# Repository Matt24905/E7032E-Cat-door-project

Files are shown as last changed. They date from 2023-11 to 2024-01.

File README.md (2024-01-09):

# E7032E-Cat-door-project
Universal low power antennas for pet microchips
<p>
  
**Project members:** <br>
Matilda Segerlund, matseg-9@student.ltu.se  <br>
Nebez Rashid, nabras-9@student.ltu.se <br>
Anders Hagström, hagane-9@student.ltu.se <br>
Agnes Lindsten, agelin-7@student.ltu.se <br>
Arvid Mattsson, arvmat-9@student.ltu.se <br>
Jakob Ekvall, jakekv-9@student.ltu.se <br>

Report to do list : https://docs.google.com/spreadsheets/d/1z1Jb6kbTAtdWHH0EG9lIYJ78wvPaeEFzT7mHL56cxgM/edit?usp=sharing

Link to report: [https://www.overleaf.com/read/vsyjcxfwmcch](https://www.overleaf.com/read/vsyjcxfwmcch) <br>

Link to presentation: https://docs.google.com/presentation/d/1uJuHqVPSid_aY_8UZ3XwjzQQK3nhx3rkxRstLh7R2MM/edit?usp=sharing

Link to WBS/project plan: https://docs.google.com/spreadsheets/d/1j_RC8x2nzi24WwkHtlm5jIMLNItzt1e427vKWdE4rbc/edit?usp=sharing <br>

**Background:** <br>
Since the mid-80's, microchip implants have been used in pets and livestocks to identify them. These implements are a little larger than a rice grain. They are passive RFID chips that must be remotely powered to receive the identification information. They are progressively been required by law. <br>

Beside legal identification, these microchips can be used to identify a pet when they want to be fed (i.e., not allow an obese pet to over eat) or to let them enter or exit their home. The latter prevents "foreign" cats to enter homes where they have no business to be in. <br>

There is a problem when the orientation of the scanner's antenna and the microchips are not aligned. The pet doors and feeders are battery powered and fixed. The former results in not enough power to retrieve the information, while the latter could have been a solution by rotating the antenna (or chip inside the pet). <br>

**Objective:** <br>
The project is simply to design a low power antenna that allows the microchip to be read whatever is its relative orientation. <br>

**Key features:** <br>
* **Compatibility:** The solution must be ISO 11784 and ISO 11785 compliant. That is, it must be able to be optimized for 134.2 kHz, but should also be able to read at 125 kHz for US microchips.
* **Low power:** The cat door should work 6 months on four AA batteries.
* **Size:** It should fit in a pet door.
* **Temperature:** It should function in temperatures from -20°C to 60°C.
* **Internet ready:** The solution should be able to integrate a secured solution that connects to the Internet. This could include near field communication (NFC), bluetooth, and WiFi solutions. 

</p>

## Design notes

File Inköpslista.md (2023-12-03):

| Date | Item |Amount | Link | Approved/ordered | Received | 
|---|---|---|---|---|---|
| 3/10 |Raspberry Pico W | 2 |https://www.electrokit.com/produkt/raspberry-pi-pico-wh/ | <ul><li>[X] </li></ul>  | <ul><li>[X] </li></ul> | 
| 6/10 |Antenna wire | 1 |[https://www.elfa.se/sv/koppartrad-008mm-o0-1mm-200g-block-cul-200-10/p/15550334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](https://www.elfa.se/sv/koppartrad-2mm-o0-5mm-200g-block-cul-200-50/p/15550340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) | <ul><li>[x] </li></ul>  | <ul><li>[x] </li></ul> | 
| 6/10 |PCB  things from Farnell |34 items| I send an email with the basket and its also on git as "ShoppingBasket" | <ul><li>[x] </li></ul>  | <ul><li>[x] </li></ul> | 
| 30/10 |OP amp rekommenderad |1 items| https://se.farnell.com/microchip/mcp6l01ut-e-ot/ic-op-amp-1-0mhz-1-8v-sot23-5/dp/1852141?st=mcp6l01 | <ul><li>[x] </li></ul>  | <ul><li>[x] </li></ul> | 
| 30/10 |OP amp till breadboard |1 items| https://se.farnell.com/texas-instruments/lm358p/ic-op-amp-dual-dip8-358/dp/3117074?st=lm358  | <ul><li>[x] </li></ul>  | <ul><li>[x] </li></ul> | 
| 25/11 |ATtiny85 |1 items| [ ATTINY85 Farnell ](https://se.farnell.com/microchip/attiny85-20pu/mcu-8bit-attiny-20mhz-dip-8/dp/1455162?st=attiny)  | <ul><li>[x] </li></ul>  | <ul><li>[x] </li></ul> | 
| 03/12 |ATtiny84 |1 items| [ ATTINY84 Farnell ](https://se.farnell.com/microchip/attiny84a-pu/mcu-8bit-attiny-20mhz-dip-14/dp/1972172?st=attiny84)  | <ul><li>[x] </li></ul>  | <ul><li>[x] </li></ul> | 
| 03/12 |BJT |5 items| [ 2N3904 Farnell ](https://se.farnell.com/multicomp/2n3904/transistor-npn-to-92/dp/1574370?st=2n3904)  | <ul><li>[x] </li></ul>  | <ul><li>[x] </li></ul> | 

Företag som vi kan beställa ifrån: <br>
https://se.farnell.com/ <br>
https://www.rs-online.com/ <br>
https://www.elfa.se/sv/<br>

Ifall det inte finns på någon av de övre. <br>
https://www.digikey.se/en

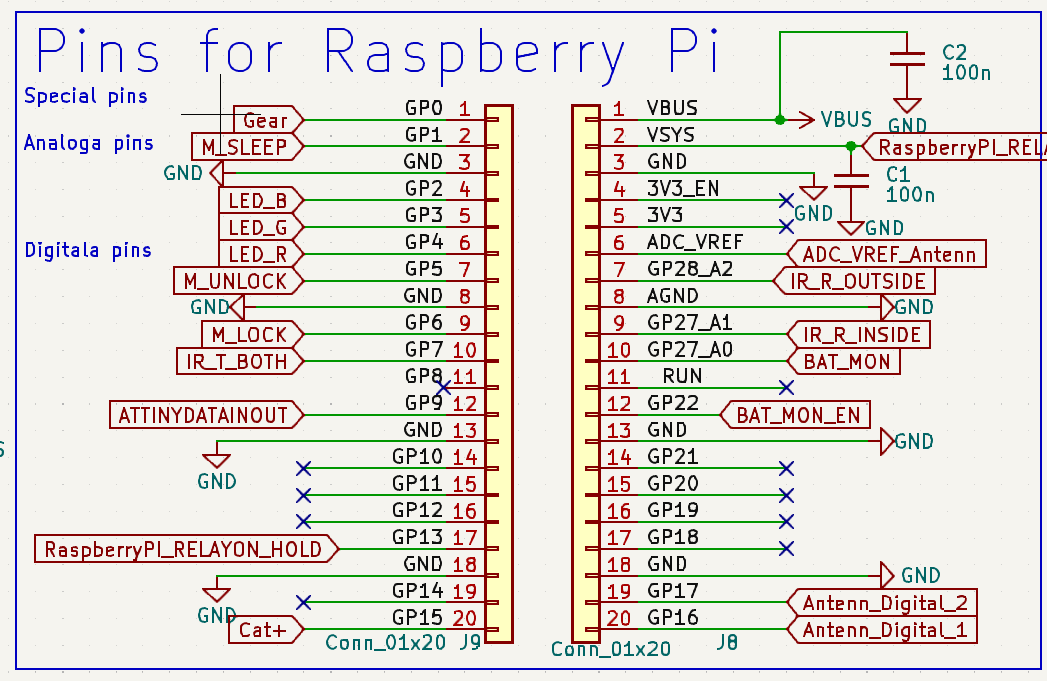
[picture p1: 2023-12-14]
Hardware/kicad.PNG

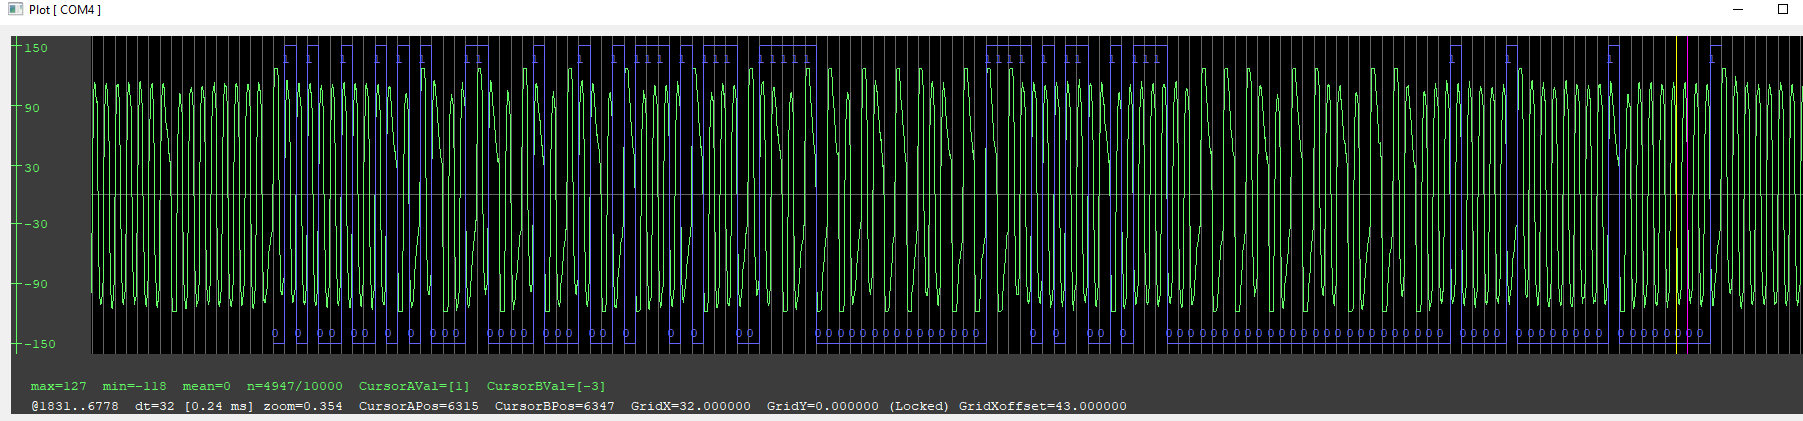
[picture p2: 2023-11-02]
Software/Proxmark3/Petchip read proxmark3 PLOT.PNG

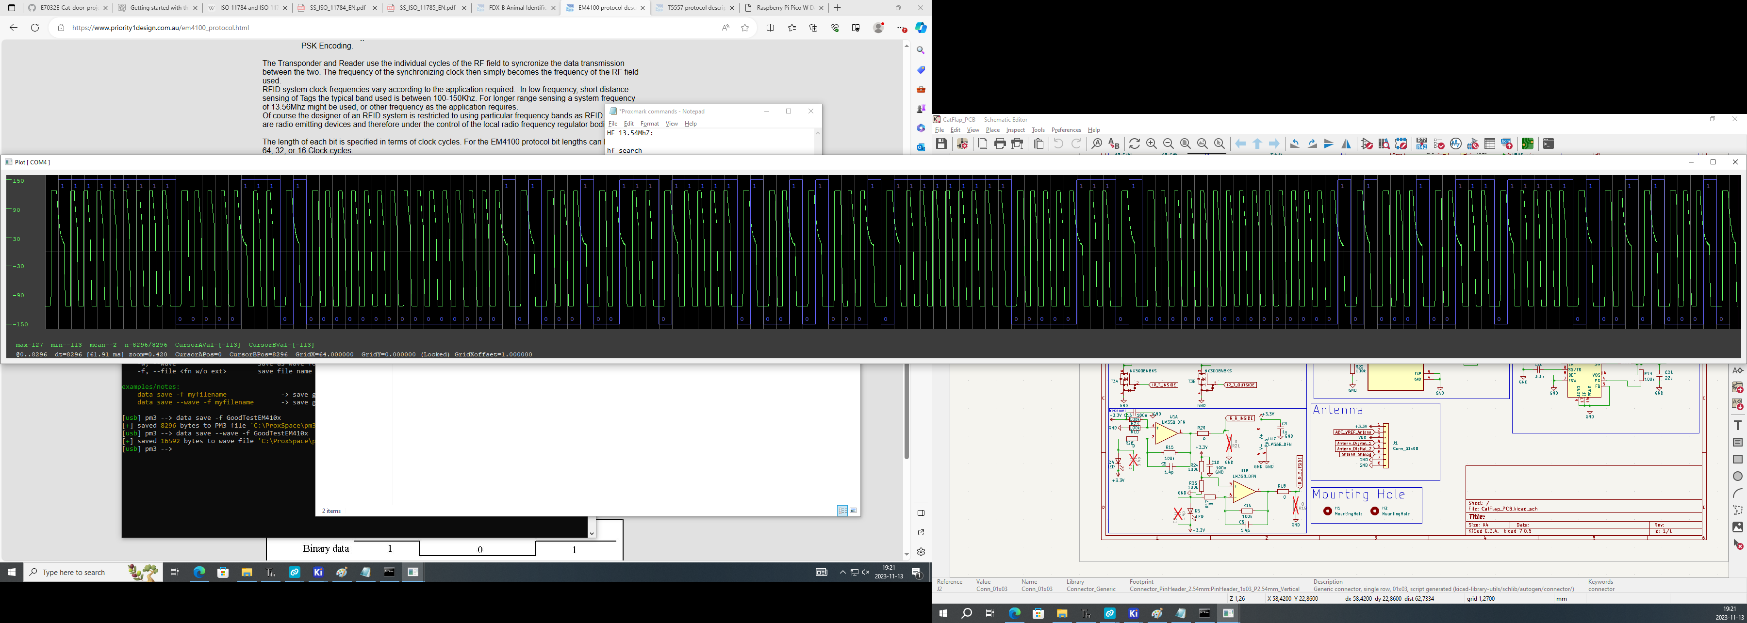
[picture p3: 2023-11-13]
Software/Proxmark3/Paint image of GoodEm410x file.png

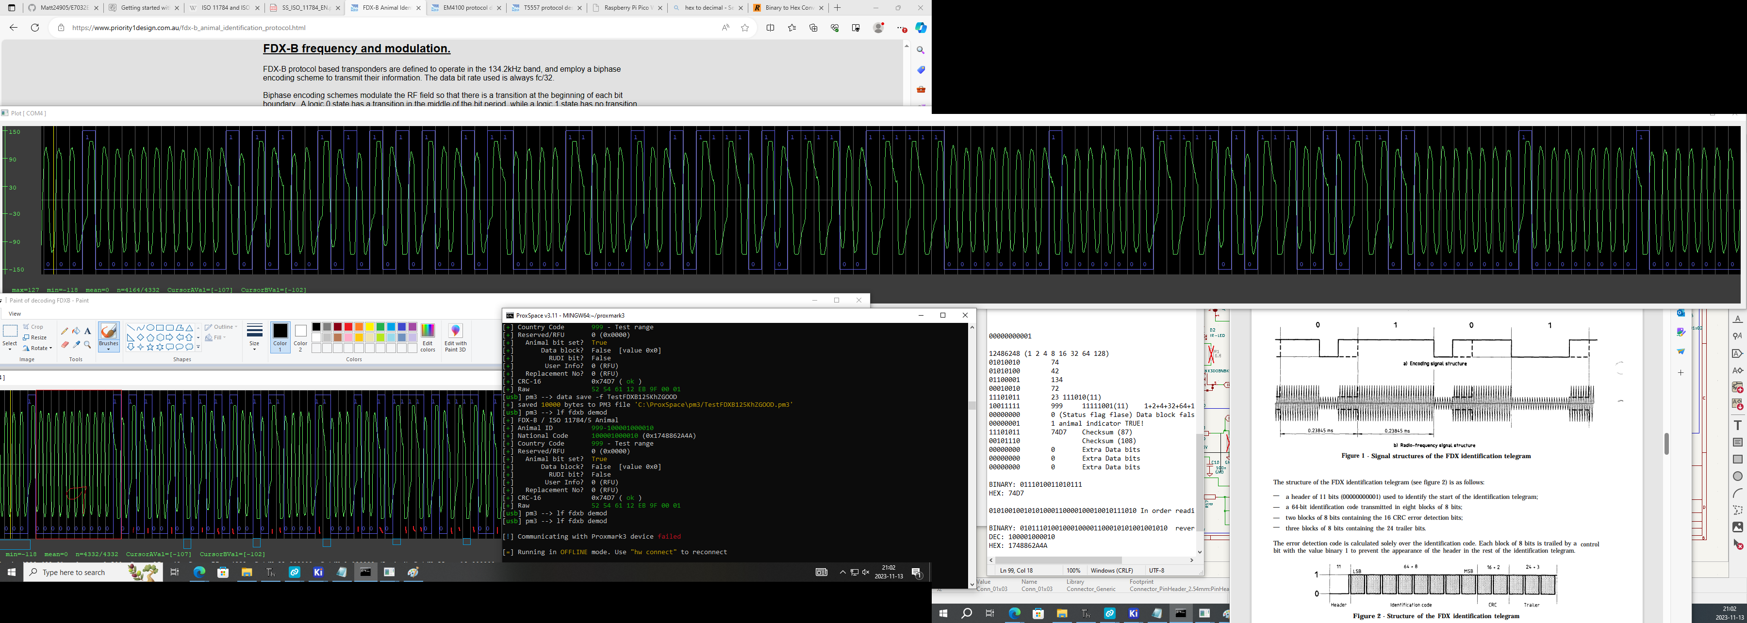
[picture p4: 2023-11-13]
Software/Proxmark3/EVERYTHING FDXB.png

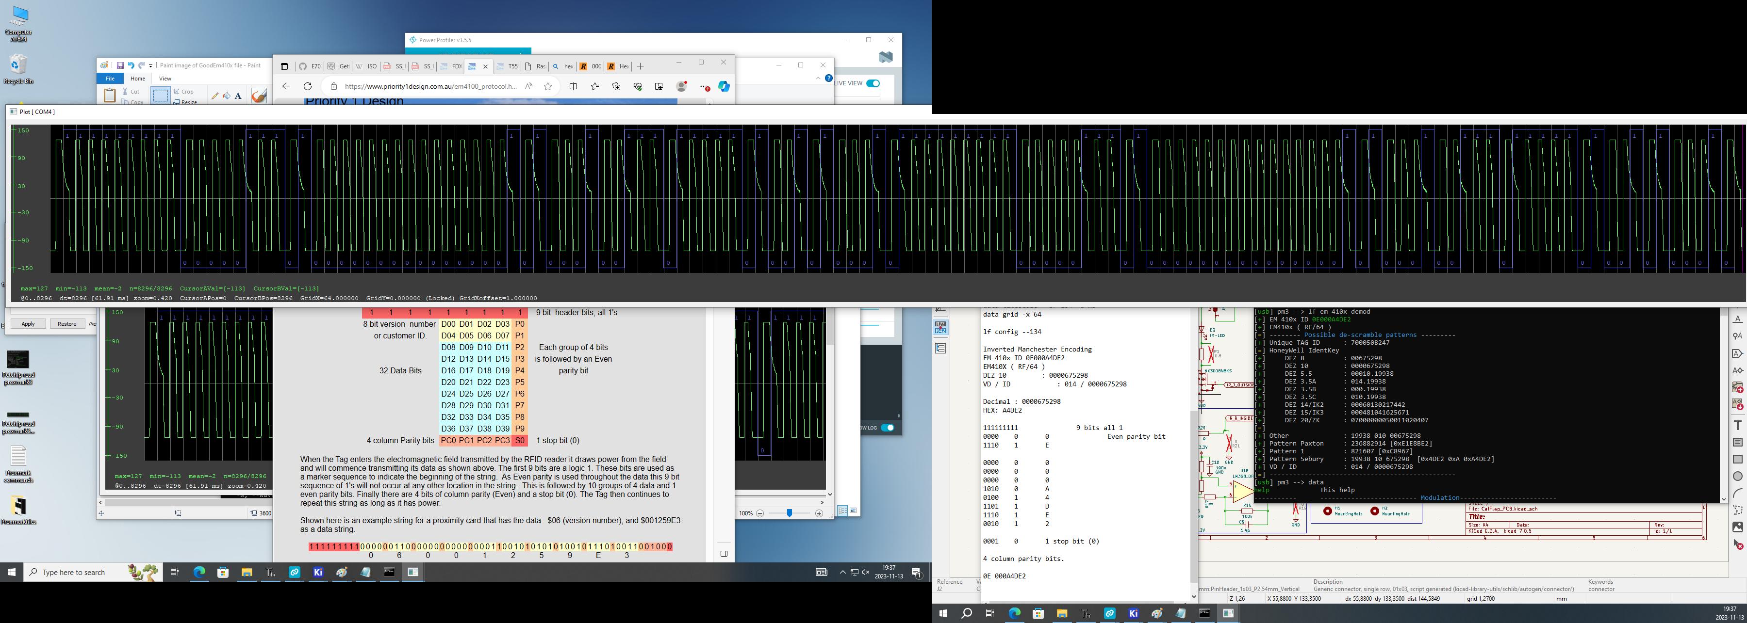
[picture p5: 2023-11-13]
Software/Proxmark3/Paint image of GoodEm410xdata EVERYTHING.png

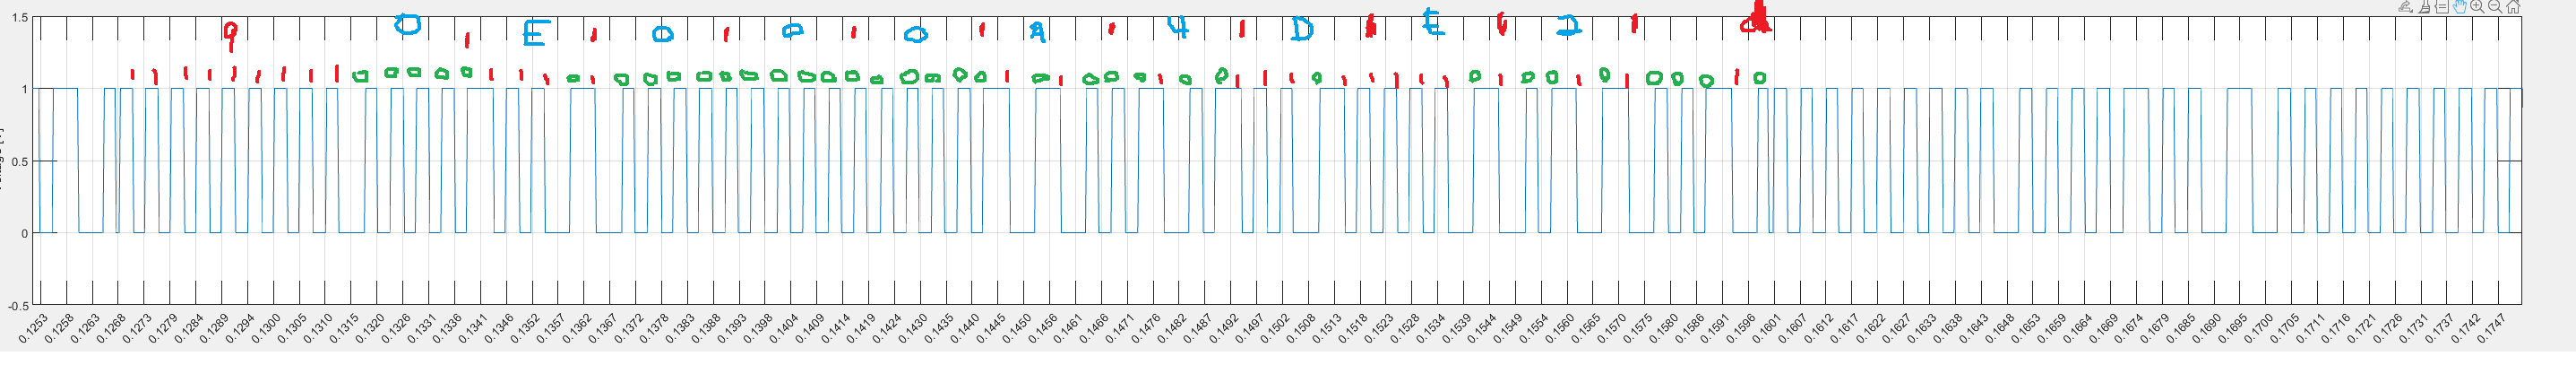
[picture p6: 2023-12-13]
Software/Matlab/em_txt file as 0E000A4DE2.png

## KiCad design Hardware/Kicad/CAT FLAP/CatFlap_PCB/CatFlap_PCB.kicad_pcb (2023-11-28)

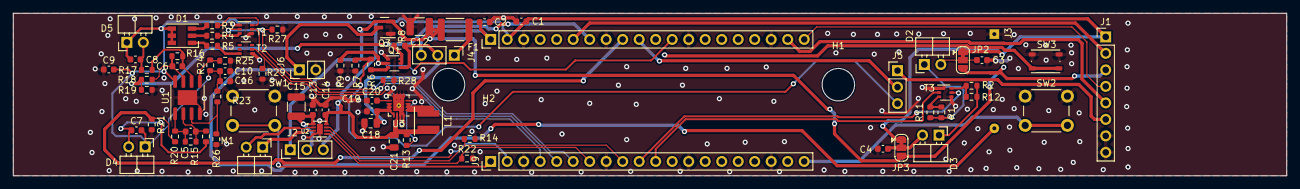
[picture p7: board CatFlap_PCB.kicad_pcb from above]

Board: 2 copper layers, 196.0 x 25.0 mm, 79 parts (0 on the bottom side), 54 nets.

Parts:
C1, C2, C10, C13, C14, C16, C19: 100n; C_0603_1608Metric
C3, C4, C9: 1u; C_0603_1608Metric
C5, C6, C7, C8: 1.4p; C_0603_1608Metric
C12, C15: 100u; C_1210_3225Metric
C18: 10u; C_0805_2012Metric
C20: 3.3n; C_0603_1608Metric
C21: 22u; C_0805_2012Metric
D1: LED_RGB; LED_RGB_PLCC-6
D2, D3: IR-LED; PinHeader_1x02_P2.54mm_Horizontal
D4, D5: LED; PinHeader_1x02_P2.54mm_Horizontal
F1: Polyfuse; Fuse_1812_4532Metric
H1, H2: MountingHole; MountingHole_5mm
J1: Conn_01x08; PinHeader_1x08_P2.54mm_Vertical
J2, J5: Conn_01x03; PinHeader_1x03_P2.54mm_Vertical
J3: Battery pack; BatteryHolder_MPD_BH-18650-PC2
J4: Conn_01x03_Socket; PinHeader_1x03_P2.54mm_Vertical
J6: Conn_01x02; PinHeader_1x02_P2.54mm_Vertical
J8, J9: Conn_01x20; PinHeader_1x20_P2.54mm_Vertical
JP2, JP3: SolderJumper_3_Bridged12; SolderJumper-3_P1.3mm_Bridged12_RoundedPad1.0x1.5mm
L1: 2.2u; L_Coilcraft_XxL4020
M1: Motor_DC; PinHeader_1x02_P2.54mm_Horizontal
Q1: NX3008CBKS; SOT-363_SC-70-6
Q3: Q_PMOS_GSD; SOT-23
R1, R2, R11, R12: 6.8; R_0603_1608Metric
R3: 68; R_0603_1608Metric
R4: 22; R_0603_1608Metric
R5: 10; R_0603_1608Metric
R6, R27, R28, R29: 330k; R_0603_1608Metric
R7: 220k; R_0603_1608Metric
R8, R9: 1meg; R_0603_1608Metric
R10, R17, R18, R19, R20, R21: 0; R_0603_1608Metric
R13, R14, R15, R16, R22, R23, R24, R25, R26: 100k; R_0603_1608Metric
SW1, SW2: SW_Push; SW_PUSH_6mm_H4.3mm
SW3: SW_Push; SW_Push_1P1T_NO_Vertical_Wuerth_434133025816
T1, T2, T3: NX3008NBKS; SOT-363_SC-70-6
U1: LM358_DFN; SOIC-8-1EP_3.9x4.9mm_P1.27mm_EP2.29x3mm
U2: DRV8837DSGR; SON50P200X200X80-9N
U3: TPS62132; VQFN-16-1EP_3x3mm_P0.5mm_EP1.68x1.68mm_ThermalVias

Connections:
+3.3V: C1.2, C7.2, C8.2, C9.2, C10.2, C14.2, C16.2, C21.2, D1.4 (BA), D1.5 (GA), D1.6 (RA), D4.1 (K), D5.1 (K), J1.1, J2.3, J8.2, JP2.1 (A), JP3.1 (A), L1.2, R13.2, R23.1, R24.1, U1.8 (V+), U2.8 (VCC), U3.14 (VOS)
/GP27_A0: J5.2, J8.10
ADC_VREF_Antenn: J1.2, J8.6
Antenn_Analog: J1.6, J5.1
Antenn_Digital_1: J1.4, J8.20
Antenn_Digital_2: J1.5, J8.19
BAT_MON: J5.3, R6.2, R7.1
BAT_MON_EN: J8.12, Q1.2 (G), R9.1
Cat+: J9.20, SW2.2
GND: C1.1, C2.1, C3.1, C4.1, C9.1, C10.1, C12.1, C13.1, C14.1, C15.1, C16.1, C18.1, C19.1, C20.2, C21.1, J1.7, J1.8, J3.1 (GND), J6.2, J8.3, J8.8, J8.13, J8.18, J9.3, J9.8, J9.13, J9.18, Q1.1 (S), Q3.1 (G), R7.2, R9.2, R14.2, R19.2, R21.2, R22.1, R25.2, R26.1, R27.1, R28.1, R29.1, SW1.1, SW2.1, SW3.1, T1.1, T1.4, T2.1, T3.1, T3.4, U1.4 (V-), U1.9 (PAD), U2.4 (GND), U2.9 (EXP), U3.5 (FB), U3.6 (AGND), U3.7 (FSW), U3.8 (DEF), U3.15 (PGND), U3.16 (PGND), U3.17 (EP)
Gear: J9.1, SW1.2
IR_R_INSIDE: J8.9, R20.1, R21.1
IR_R_OUTSIDE: J8.7, R18.1, R19.1
IR_T_INSIDE: J9.11, T3.2
IR_T_OUTSIDE: J9.10, T3.5
LED_B: J9.4, R29.2, T2.2
LED_G: J9.5, R28.2, T1.5
LED_R: J9.6, R27.2, T1.2
M_LOCK: J9.9, R14.1, U2.6 (IN1)
M_SLEEP: J9.2, U2.7 (~SLEEP)
M_UNLOCK: J9.7, R22.2, U2.5 (IN2)
unnamed: C5.1, R15.1, R20.2, U1.1
unnamed: C6.1, R16.1, R18.2, U1.7
unnamed: D1.3 (BK), R3.2
unnamed: D1.2 (GK), R4.2
unnamed: D1.1 (RK), R5.2
unnamed: C3.2, D2.2 (A), JP2.2 (C)
unnamed: D2.1 (K), R1.2, R11.2
unnamed: C4.2, D3.2 (A), JP3.2 (C)
unnamed: D3.1 (K), R2.2, R12.2
unnamed: C7.1, D4.2 (A), R10.2
unnamed: C8.1, D5.2 (A), R17.2
unnamed: C13.2, C15.2, J2.2, U2.1 (VM)
unnamed: J3.2 (V+), J6.1, Q3.3 (D)
unnamed: F1.1, J4.1
unnamed: L1.1, U3.1 (SW), U3.2 (SW), U3.3 (SW)
unnamed: M1.1 (+), U2.3 (OUT2)
unnamed: M1.2 (-), U2.2 (OUT1)
unnamed: Q1.5 (G), Q1.6 (D), R8.2
unnamed: Q1.3 (D), R6.1
unnamed: R1.1, R11.1, T3.3
unnamed: R3.1, T1.6
unnamed: R4.1, T1.3
unnamed: R5.1, T2.6
unnamed: R2.1, R12.1, T3.6
unnamed: R23.2, R26.2, U1.3 (+)
unnamed: C5.2, R10.1, R15.2, U1.2 (-)
unnamed: R24.2, R25.1, U1.5 (+)
unnamed: C6.2, R16.2, R17.1, U1.6 (-)
unnamed: R13.1, U3.4 (PG)
unnamed: C20.1, U3.9 (SS/TR)
VBUS: C2.2, J4.3, J8.1
VDD: C12.2, F1.2, J1.3, J2.1, JP2.3 (B), JP3.3 (B), Q3.2 (S)
V_BAT: C18.2, C19.2, J4.2, Q1.4 (S), R8.1, U3.10 (AVIN), U3.11 (PVIN), U3.12 (PVIN), U3.13 (EN)

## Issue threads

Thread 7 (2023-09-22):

Goals for midterm presentation

Matt24905, 2023-09-22:
- [ ] Prototypkrets för antennen, inducera fält och ta emot enklare information
- [ ] Power management
- [ ] PCB-design
- [ ] Börja kolla på app, mjukvarulösningar och databas
- [ ] IR, knapp och motor ska fungera som tänkt, både hårdvaru- och mjukvarumässigt
- [ ] Skriva rapport för alla delar vi gjort
- [ ] Mer mätningar på antennen och motorn (är motorn mer strömsnål? Vilka är antennens blind spots?)
- [ ] Göra en testuppställning för antennen

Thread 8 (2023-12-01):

Saker som är kvar att fixa i mjukvara (bygg på as you go...)

Matt24905, 2023-12-01:
- Antenn
- IR sensorer
- Ta bort katt från app
- Lägg till katt från app
- Köra addCat endast efter IR och antenn läst katt
- Köra removeCat endast efter IR och antenn läst katt, ELLER när ägaren tar bort i appen
- En till databas för entry/exit? Eller ha allt i samma?
- Visualisera från databas

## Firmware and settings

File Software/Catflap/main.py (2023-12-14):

import time
from machine import Pin
from fakeData import *
from helpers import *
from connect import connectToWifi
from secrets import ssid, password
from buttons import *
import readtag.py
connectToWifi(ssid, password)

while True:
    #IR_sensor_reading = False
    if button3.value() == 0:
        print("You made it")
        #nuvarande kollar endast ifall en tag är där eller ej, returnerar true/false
        read_tag(pin_number=1, num_measurements=8000, delay_between_measurements_us=1,antenna_pin=0)
        pass
    elif button1.value() == 1 and button2.value() == 1:
        pass
    elif button1.value() == 0 and button2.value() == 1:
        addCat()
        blink(led1)
        pass
    elif button2.value() == 0 and button1.value() == 1:
        checkIfCat()
        blink(led3)
        pass
    else:
        print("Nothing is happening, I'm dying from boredom")

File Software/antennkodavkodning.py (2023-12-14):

def read_file(filename):
    with open(filename, "r") as file:
        data_list = []
        for line in file:
            elements = line.strip().split(',')  # Change delimiter if needed
            converted_elements = [int(elem) for elem in elements]
            data_list.append(converted_elements)
        return data_list

def find_transition_indices(data):
    transition_indices = []
    for i in range(1, len(data)):
        if data[i] != data[i - 1]:
            transition_indices.append(i)
    return transition_indices

def find_1_to_0_transitions(data):
    transitions_1_to_0 = []
    for i in range(1, len(data)):
        if data[i - 1][0] == 1 and data[i][0] == 0:
            transitions_1_to_0.append(i)
    return transitions_1_to_0

def calculate_median(lst):
    n = len(lst)
    s = sorted(lst)
    return (s[n//2-1]/2.0+s[n//2]/2.0, s[n//2])[n % 2] if n else None

def process_data(data_list, transition_indices, transitions_1_to_0):
    approx_step = round(calculate_median([transition_indices[i] - transition_indices[i - 1] for i in range(1, len(transition_indices))]) * 1.15)
    
    transistion_counter = 0
    delbit = []
    delbitkoord = []
    i = 0
    flat_data_list = [item for sublist in data_list for item in sublist]
    
    while i < len(flat_data_list):
        segment_start = i
        if segment_start >= transition_indices[transistion_counter]:
            segment_start = transition_indices[transistion_counter]
            transistion_counter += 1
        
        segment_end = segment_start + approx_step
        segment_data = sum(flat_data_list[segment_start:segment_end])
        segment_data /= approx_step
        
        if segment_end > len(flat_data_list):
            break
        
        i = segment_end
        delbitkoord.append(segment_start)
        
        if segment_data > 0.4:
            delbit.append(1)
        else:
            delbit.append(0)
    
    return delbit, delbitkoord, transition_indices


def find_start_of_pattern(signal, pattern):
    signal_str = ''.join(map(str, signal))  # Convert the signal list to a string
    pattern_str = ''.join(map(str, pattern))  # Convert the pattern list to a string
    
    start_index = signal_str.find(pattern_str)
    
    if start_index != -1:
        return start_index + len(pattern_str)
    else:
        return -1  # Return -1 if the pattern is not found

def decode_manchester_signal(signal):
    pattern = [1, 1, 0, 1, 0, 1, 0, 1, 0, 1, 0, 1, 0, 1, 0, 1, 0, 1, 0]  # Define the pattern to search for
    start_index = find_start_of_pattern(signal, pattern)
    print(start_index)
    start_index = start_index - 18
    
    if start_index != -1:
        print('start found')
        encoded_signal = signal[start_index:len(signal)]
        
    decoded_binary = []  # Initialize an empty list to store the decoded binary sequence

    for i in range(0, len(encoded_signal), 2):  # Processing pairs of values (each pair represents one bit)
        current_bit = encoded_signal[i:i + 2]  # Extracting the current pair (each pair represents one bit in Manchester)

        if current_bit == [0, 1]:  # Decoding '01' to '0' in binary
            decoded_binary.append('0')
        elif current_bit == [1, 0]:  # Decoding '10' to '1' in binary
            decoded_binary.append('1')
        #else:
            
            #decoded_binary.append('2')
            #return "Invalid Manchester encoding sequence", ''  # Return an error for invalid sequence

    return ''.join(decoded_binary)  # Return the decoded binary sequence as a string
        

def EM410Protocol(output_array):
    # Convert output_array to a string
    #output_string = ''.join(map(str, output_array))
    output_string = output_array
    # Define the header pattern
    header_pattern = "111111111"

    # Find the starting position of the header pattern
    start_index = output_string.find(header_pattern)

    if start_index != -1:
        # Move past the header pattern
        start_index += len(header_pattern)

        hex_values = []  # Initialize an empty list to store hex values

        # Check 5-bit sequences and their even parity 10 times
        for _ in range(10):
            current_sequence = output_string[start_index:start_index + 5]

            if len(current_sequence) == 5:
                ones_count = current_sequence.count('1')
                is_even_parity = ones_count % 2 == 0

                # Decode the first 4 bits to hexadecimal and append to the hex_values list
                hex_val = hex(int(current_sequence[:4], 2))[2:].upper()
                hex_values.append(hex_val)

            else:
                return "Incomplete sequence of 5 bits", ''.join(hex_values)  # Return incomplete sequence error

            start_index += 5  # Move to the next 5-bit sequence

        hex_string = ''.join(hex_values)  # Concatenate the hex values into a single string

        if output_string[start_index + 4] == '0':
            hex_string = ''.join(hex_values)
            return None, hex_string
        else:
            return "Stop bit mismatch", ''.join(hex_values)

    else:
        return "Header pattern not found", ''
# 
# from machine import Pin
# import utime
# 
# from machine import Pin
# import utime
# from machine import Pin
# 
# 
# def read_after_starting_sequence(pin, starting_sequence, sample_rate_us):
#     sequence_to_detect = [1,1,0, 1, 0, 1, 0,1,0,1,0,1,0,1,0,1,0]  # Sequence to detect: alternating high and low
# 
#     while True:
#         readings = []  # Store the sequence of readings
#         for _ in range(len(sequence_to_detect)):
#             readings.append(pin.value())  # Read pin values and store in 'readings'
# 
#         if readings == sequence_to_detect:
#             print("Detected the sequence!")
#             break  # Exit the loop if the sequence is detected
#         if buffer.startswith(starting_sequence):
#             # Perform actions once the starting sequence is detected
#             print("Starting sequence detected!")
#             started_reading = True  # Set flag to start reading
#             buffer_pos = 0  # Reset buffer position
# 
#         if started_reading:
#             # Process or handle the data after the starting sequence is detected
#             # Here, you can add your logic to read or process the incoming data
#             # For example, print the data or trigger specific actions
# 
#             # For demonstration, print the buffer content after starting sequence detection
#             print("Data after starting sequence:", buffer[buffer_pos:])
#             # Add your logic here to process or use the data
#             data_list = buffer[buffer_pos:]
#             transition_indices = find_transition_indices(data_list)
#             transitions_1_to_0 = find_1_to_0_transitions(data_list)
#             
#             delbit, delbitkoord, transition_indices = process_data(data_list, transition_indices, transitions_1_to_0)
#
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

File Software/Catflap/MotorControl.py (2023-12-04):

from machine import Pin, Timer
import time

motor1 = Pin(5, Pin.OUT)
motor2 = Pin(6, Pin.OUT)
Motor_Sleep = Pin(1, Pin.OUT) # Motor Sleep pin 

def Unlock():
    Motor_Sleep.on()	# Turn on the H-Bridge IC.	Has a wake time of 30us.
    motor1.on()			# Enable one pin of the Motor control to make it spin in one direction.
    time.sleep(0.07)	# Delay 70ms in order to make sure the motor have the time to Unlock/Lock.
    turnOff(motor1)		# Turn off one pin of the motorControl to make it stop.
    Motor_Sleep.off()	# Turn off the H-Bridge IC.
    
def Lock():
    Motor_Sleep.on()
    motor2.on()
    time.sleep(0.07)
    turnOff(motor2)
    Motor_Sleep.off()
    
def Unlock_Lock(LockDelay):
    Motor_Sleep.on()
    motor1.on()
    time.sleep(0.07)
    turnOff(motor1)
    time.sleep(LockDelay)	# Uncertain about sleep in the entire system. Make better when know what to do.
    motor2.on()
    time.sleep(0.07)
    turnOff(motor2)
    Motor_Sleep.off()    
    
def turnOff(motor):
    motor.off()

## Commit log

2023-11-01 Create power monitoring
2023-11-02 Update buttons.py
    Ugly code less ugly
2023-11-14 New measurement with Johan of the Proxmark3
    [em410_2023-11-14_0_143751.csv]
2023-11-28 Fixed things from first rev of PCB
    [CatFlap_PCB.kicad_pcb, CatFlap_PCB.kicad_sch]
2023-11-30 update matlab and python script
    [BatteryMonitor Standalone.csv]
2023-12-04 Updated MotorControl
